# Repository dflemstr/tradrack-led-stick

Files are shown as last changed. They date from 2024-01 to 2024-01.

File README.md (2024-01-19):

# Tradrack LED stick

This is a mod for Annex Engineering's [TradRack][1] that enables the addition
of LED light indicators for each filament gate/lane.

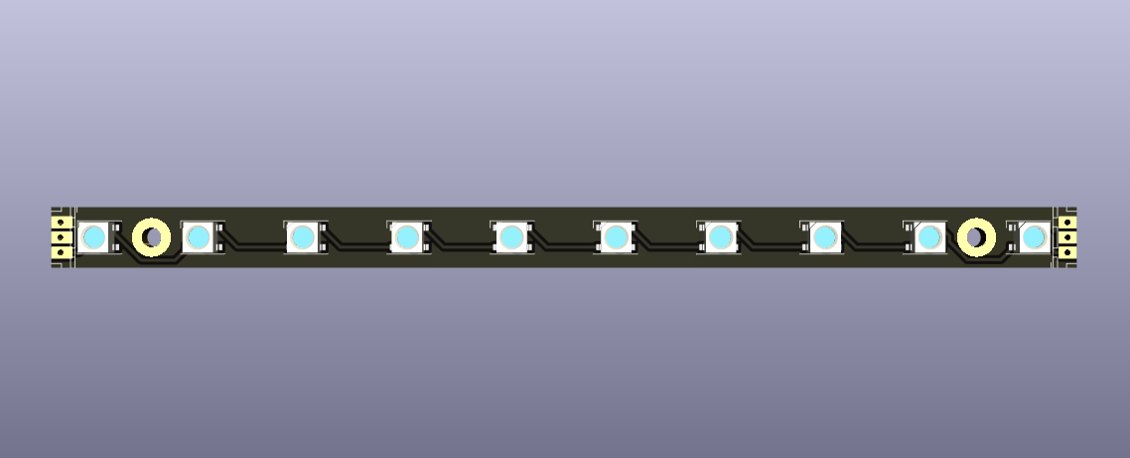
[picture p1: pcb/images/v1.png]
Rendered image of the v1 PCB


Since the lanes are spaced at a 17mm pitch, there are no regular LED strips
that would fit a Tradrack with a large number of lanes (I myself use ~35 lanes),
hence the need for this project.

This project is not an official Annex Engineering project and bears no
affiliation with the Annex Engineering organization.  The project is licensed
under the terms of GPL-3.

There are various software options available for controlling these LEDs,
for example by using the [Happy Hare][2] software to control the Tradrack.

For now there's only a PCB design in this repo.  I might eventually add
some 3D-printable parts that aid in mounting the LED boards.

## Fabrication

You can easily get the PCBs fabricated at various PCB shops.  I provide
easy-to-use files for fabrication using [JLCPCB][3] in the `pcb/fabrication-outputs` folder.
Simply upload the files to JLCPCB's assembly service and everything
should mostly just work.

## Mounting

The PCBs are designed with a 17mm pitch which should match the Tradrack lane
spacing.  You can join the PCB with a short piece of wire, a solder bridge,
or a JST-XH straight-through connector.  The PCBs are designed with a 1mm
gap between them to allow for some adjustment when aligning multiple PCBs,
in case the lanes or the PCBs themselves have some imperfections.

**Note**: The LED stick is designed to be adaptable to the [Voron Daylight Disco][4]
pinout.  However, due to space constraints (because the stick needs to maintain the
17mm spacing), there isn't enough room on the board to solder a "normal" or "flipped"
JST-XH connector.  Instead, take a vertical JST-XH connector, and bend the legs 90 degrees
towards the side of the connector housing that has 2 slots.  Then, solder the connector from
above onto the LED stick, letting it hang out over the side of the board.  If done
correctly, the board will be pin-compatible with the Voron Daylight Disco board.

Here are some photos of a finished soldering job for reference:




The PCBs are also designed to be easy to cut at an arbitrary point without
causing a short.  Cutting the PCB between any two LEDs should be easily done
with a hack saw/rotary cutter/...  Just make sure to use appropriate protective
equipment and maybe have a spare stick in case something goes wrong.

### LED profile

I am using a LED profile to mount the LED PCBs into.  The size I'm using is
fairly common in hardware stores, with a 17mm outside width, 6.5mm thick
(without the diffuser), and has a 12mm inner channel.

To mount the PCBs this way, I used thermal double sided tape (to aid with
heat dissipation -- although it shouldn't be strictly needed) and then
the 3D printed mounting bracket in [`led-profile-holder`](./led-profile-holder).

This assembly can then be mounted at the front of the Trad Rack, in between the 2020
and the cable chain.

It is also necessary to use low-profile M5 bolts for any parts that are mounted to
the front of the Trad Rack extrusion (the `idler_pulley_mount` and `motor_mount_lower`)
if the filament lane modules are mounted in such a way that the corresponding LEDs need
to be in front of these parts. I use [OpenBuilds low profile M5 screws][5], 8mm long.

For the cable chain anchor, a lowered version is needed.  I've included one in the
[`led-profile-holder`](./led-profile-holder) directory.

There won't be any room for other front-mounted parts on the 2020 that stick out more
than 7mm.  For example, you can use [this mount][6] for an ERCF Easy BRD to mount the
board from the bottom of the extrusion instead of the side.

[1]: https://github.com/Annex-Engineering/TradRack
[2]: https://github.com/moggieuk/Happy-Hare/blob/main/doc/leds.md
[3]: https://jlcpcb.com/
[4]: https://github.com/VoronDesign/Voron-Hardware/tree/master/Daylight/Disco_on_a_stick
[5]: https://openbuildspartstore.com/low-profile-screws-m5-10-pack-/
[6]: https://www.printables.com/model/481199-ercf-easybrdcan-brd-mount-for-tr

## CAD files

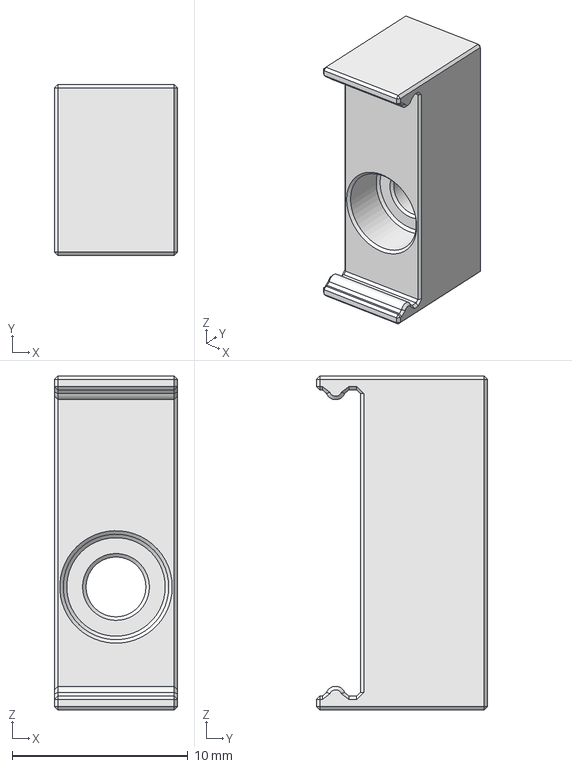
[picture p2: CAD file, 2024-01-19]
led-profile-holder/tradrack-led-profile-holder.FCStd
7.00 x 9.75 x 19.0 mm

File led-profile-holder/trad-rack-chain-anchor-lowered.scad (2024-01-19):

difference() {
    import("/mnt/data/src/github.com/Annex-Engineering/TradRack/STLs/Stationary Parts/chain_anchor_x1_rev3.STL");

    translate([14, -29, 6.8125]) cube([22, 50, 10]);
}

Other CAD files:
led-profile-holder/tradrack-led-profile-holder-body.stl

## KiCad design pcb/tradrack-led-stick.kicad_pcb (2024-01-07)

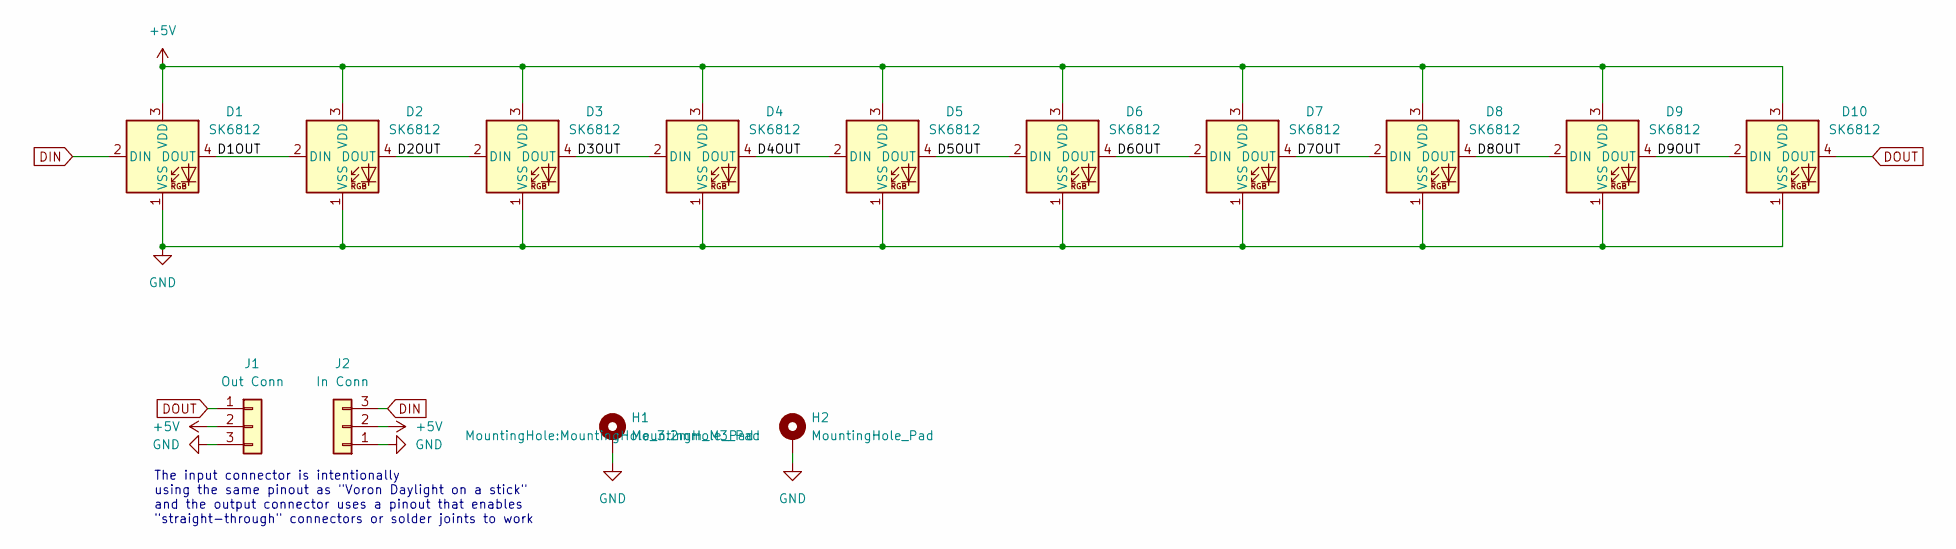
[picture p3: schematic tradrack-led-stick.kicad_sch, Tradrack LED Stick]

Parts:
D1, D2, D3, D4, D5, D6, D7, D8, D9, D10: SK6812; LED_SK6812_PLCC4_5.0x5.0mm_P3.2mm; MPN SKC6812RGBW-NW-B; LCSC C5380880
H1, H2: MountingHole_Pad; MountingHole_3.2mm_M3_Pad
J1: Out Conn; JST_XH_B3B-XH-A_1x03_P2.50mm_Vertical
J2: In Conn; JST_XH_B3B-XH-A_1x03_P2.50mm_Vertical

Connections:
+5V: D1.3 (VDD), D2.3 (VDD), D3.3 (VDD), D4.3 (VDD), D5.3 (VDD), D6.3 (VDD), D7.3 (VDD), D8.3 (VDD), D9.3 (VDD), D10.3 (VDD), J1.2, J2.2
/D1OUT: D1.4 (DOUT), D2.2 (DIN)
/D2OUT: D2.4 (DOUT), D3.2 (DIN)
/D3OUT: D3.4 (DOUT), D4.2 (DIN)
/D4OUT: D4.4 (DOUT), D5.2 (DIN)
/D5OUT: D5.4 (DOUT), D6.2 (DIN)
/D6OUT: D6.4 (DOUT), D7.2 (DIN)
/D7OUT: D7.4 (DOUT), D8.2 (DIN)
/D8OUT: D8.4 (DOUT), D9.2 (DIN)
/D9OUT: D9.4 (DOUT), D10.2 (DIN)
DIN: D1.2 (DIN), J2.3
DOUT: D10.4 (DOUT), J1.1
GND: D1.1 (VSS), D2.1 (VSS), D3.1 (VSS), D4.1 (VSS), D5.1 (VSS), D6.1 (VSS), D7.1 (VSS), D8.1 (VSS), D9.1 (VSS), D10.1 (VSS), H1.1, H2.1, J1.3, J2.1

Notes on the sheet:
The input connector is intentionally using the same pinout as "Voron Daylight on a stick" and the output connector uses a pinout that enables "straight-through" connectors or solder joints to work

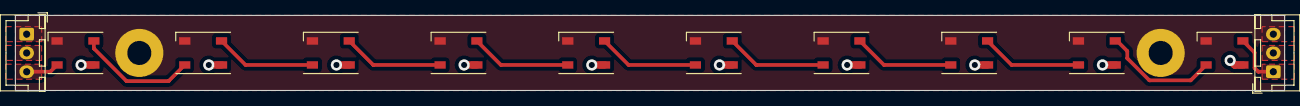
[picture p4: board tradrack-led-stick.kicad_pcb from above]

Board: 2 copper layers, 169.0 x 10.0 mm, 14 parts (0 on the bottom side), 13 nets.

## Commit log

2024-01-07 Publish v1 of the PCB
    [tradrack-led-stick.kicad_pcb, tradrack-led-stick.kicad_sch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]
2024-01-17 Remove stray kicad file
2024-01-17 Add 3D printed LED profile holder
    [tradrack-led-profile-holder-body.stl, tradrack-led-profile-holder.FCStd]
2024-01-19 Switch to a straight LED profile instead
    [trad-rack-chain-anchor-lowered.scad, tradrack-led-profile-holder-body.stl, tradrack-led-profile-holder.FCStd]
